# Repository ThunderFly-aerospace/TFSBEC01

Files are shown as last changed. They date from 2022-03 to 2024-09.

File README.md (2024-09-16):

# TFSBEC01 - High efficient power supply with measuring circuit for UAV

Many devices in unmanned vehicles require a quality power supply, and it is very useful to know the actual and real consumption of these components. Our TFSBEC module is designed to provide power to servos, autopilot (flight controller), and other medium-power drone accessories. In case the user needs more current or two independent sources on his drone, for example, a separate source for avionics and power-consuming elements (actuators), it is possible to chain these modules.

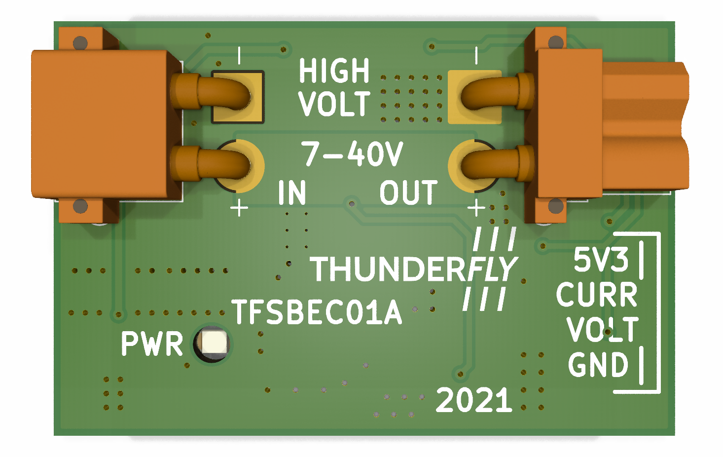
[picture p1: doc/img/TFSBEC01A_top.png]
TFSBEC01 top

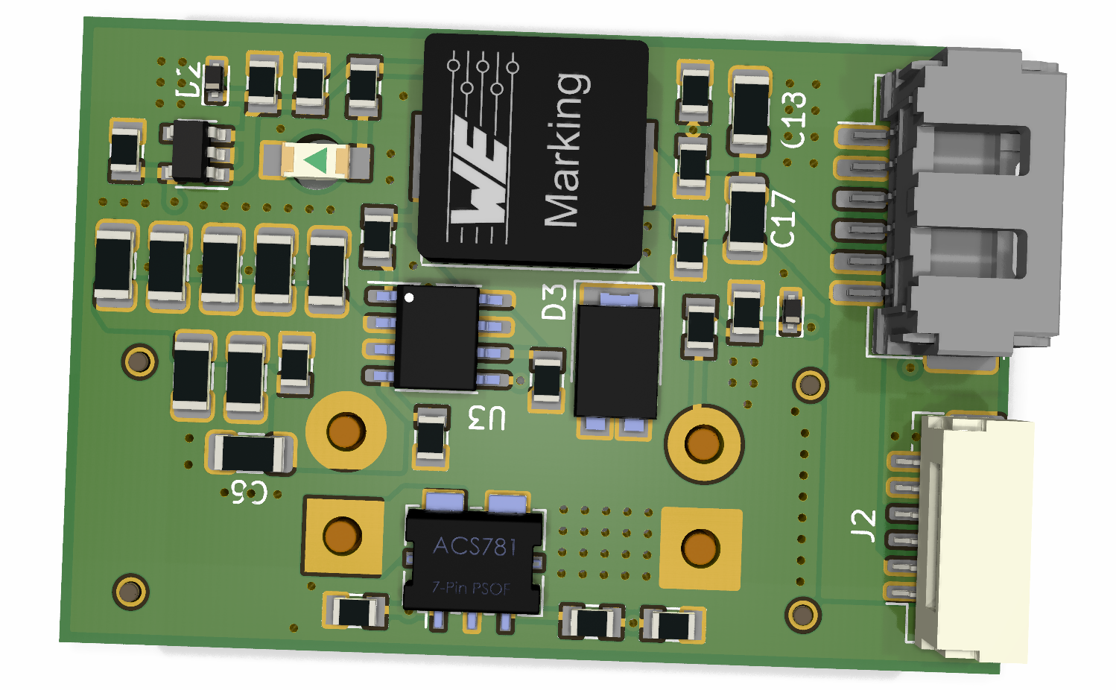
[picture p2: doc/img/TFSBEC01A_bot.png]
TFSBEC01 bottom


## Parameters

| Parameter | Value | Note |
|---|---|---|
| Regulator technology | Switched step-down| [LMR14050](https://www.ti.com/lit/ds/symlink/lmr14050.pdf)|
| Input voltage | 6 - 40 V  | Equivalent of 2S to 9S li-pol  accumulators |
| Output voltage | 5.4 V, 5 A | based form the PX4 standard, can be adjusted |
| Regulated connector | Molex Click-n-mat 6p, JST-GH 6p | Connectors are parallel |
| In/Out connector | XT30 | max current 15 A |
| Current measurement range | 0 - 50 A | |
| Volts per Amper | 39.6 mV/A | From component datasheet |
| Current measurement Volts offset | 330 mV | From component datasheet |
| Voltage measurement range | 0 - 40 V | Depend on target ADC max input ( max. 3.95 V ) |
| Voltage measurement divider | 10.13 | From schematic |
| Size | approx. 46 x 30 mm| PCB only |
| Weight | | PCB only |
| Compatibility | Pixhawk-based drones | As a quality source, it can be operated on any drone |

## PX4 Params

These constants are nominal values taken from the datasheet:

  * A = BAT1_A_PER_V = 25.2525
  * B = BAT_V_OFFS_CURR = 0.33
  * BAT1_V_DIV = 10.13
    
QGC build-in measurement can be used to estimate parameters more precisely for the specific piece. The PX4 estimation of current is calculated from the ADC raw voltage by the following formula: 

I estimate equation

For the computation of BAT_V_OFFS_CURR, multiple current measurements are usually needed, because there are significant peaks due to powering of electronics with a low current consumption.

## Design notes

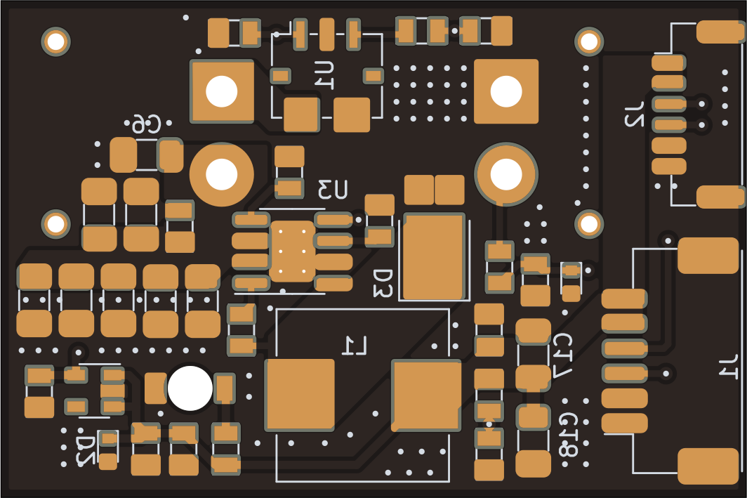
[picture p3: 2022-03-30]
doc/gen/img/pcb/TFSBEC01A-bottom.png

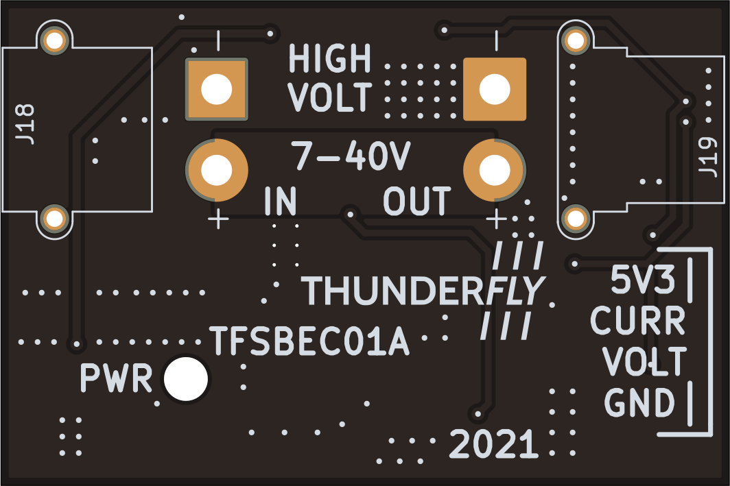
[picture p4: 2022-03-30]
doc/gen/img/pcb/TFSBEC01A-top.png

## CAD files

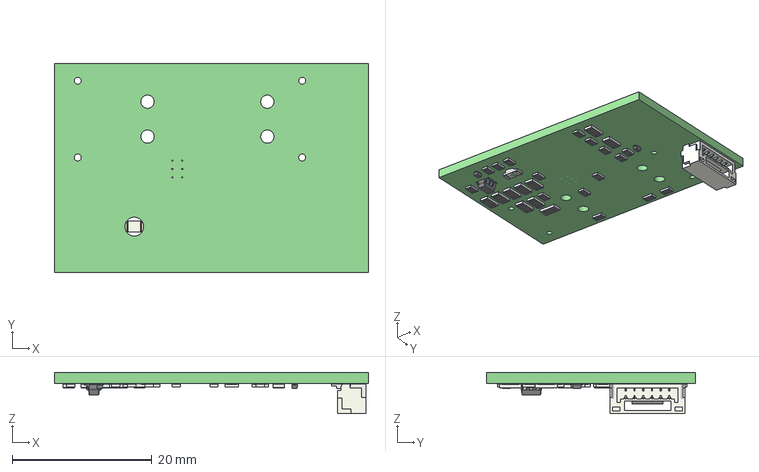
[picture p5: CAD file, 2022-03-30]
doc/gen/TFSBEC01A.step
45.0 x 30.0 x 5.89 mm
tmpdwvmqxz2 PCB

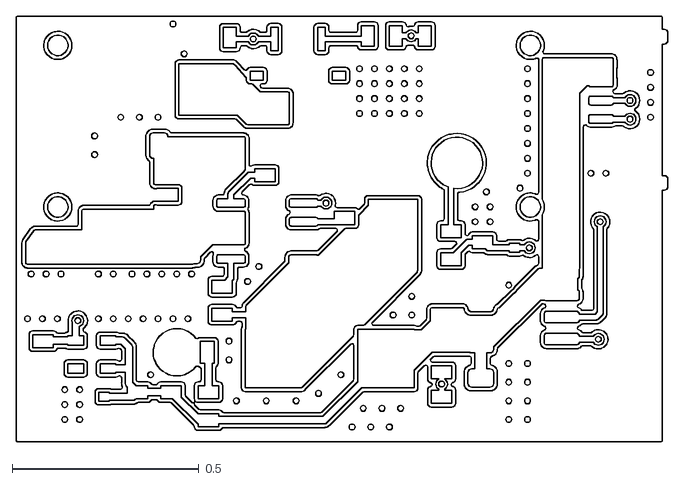
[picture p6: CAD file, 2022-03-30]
doc/gen/dxf/TFSBEC01A-B_Cu.dxf
1.75 x 1.14

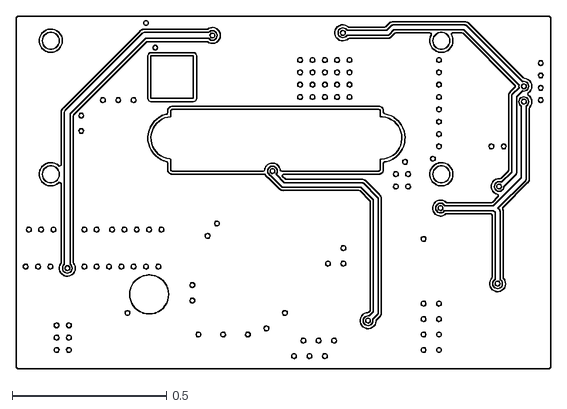
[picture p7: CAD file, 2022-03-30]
doc/gen/dxf/TFSBEC01A-F_Cu.dxf
1.73 x 1.14

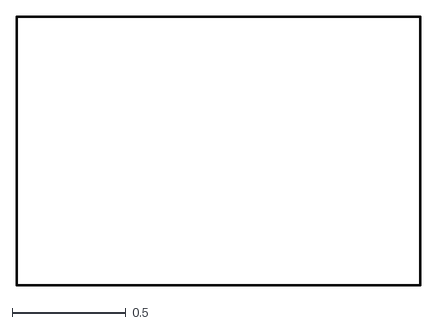
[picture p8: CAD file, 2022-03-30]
doc/gen/dxf/TFSBEC01A-Edge_Cuts.dxf
1.78 x 1.19

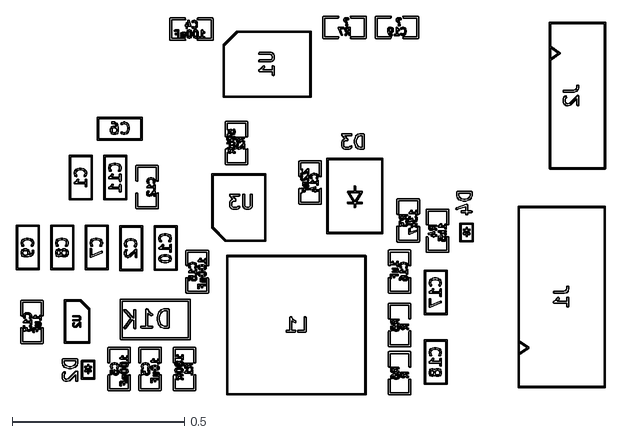
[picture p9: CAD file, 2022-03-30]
doc/gen/dxf/TFSBEC01A-B_Fab.dxf
1.71 x 1.10

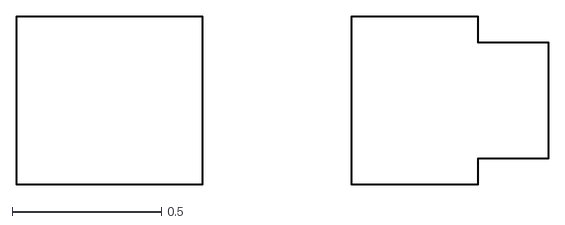
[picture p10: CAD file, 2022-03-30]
doc/gen/dxf/TFSBEC01A-F_Courtyard.dxf
1.79 x 0.565

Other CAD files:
doc/gen/dxf/TFSBEC01A-User_6.dxf
doc/gen/dxf/TFSBEC01A-User_4.dxf
doc/gen/dxf/TFSBEC01A-User_Drawings.dxf
doc/gen/dxf/TFSBEC01A-User_9.dxf
doc/gen/dxf/TFSBEC01A-User_Eco1.dxf
doc/gen/dxf/TFSBEC01A-User_8.dxf
doc/gen/dxf/TFSBEC01A-User_5.dxf
doc/gen/dxf/TFSBEC01A-User_7.dxf
doc/gen/dxf/TFSBEC01A-F_Adhesive.dxf
doc/gen/dxf/TFSBEC01A-Margin.dxf
doc/gen/dxf/TFSBEC01A-User_3.dxf
doc/gen/dxf/TFSBEC01A-User_Comments.dxf
doc/gen/dxf/TFSBEC01A-B_Adhesive.dxf
doc/gen/dxf/TFSBEC01A-B_Courtyard.dxf
doc/gen/dxf/TFSBEC01A-B_Mask.dxf
doc/gen/dxf/TFSBEC01A-B_Paste.dxf
doc/gen/dxf/TFSBEC01A-B_Silkscreen.dxf
doc/gen/dxf/TFSBEC01A-F_Fab.dxf
doc/gen/dxf/TFSBEC01A-F_Mask.dxf
doc/gen/dxf/TFSBEC01A-F_Paste.dxf
doc/gen/dxf/TFSBEC01A-F_Silkscreen.dxf
doc/gen/dxf/TFSBEC01A-User_1.dxf
doc/gen/dxf/TFSBEC01A-User_2.dxf
doc/gen/dxf/TFSBEC01A-User_Eco2.dxf

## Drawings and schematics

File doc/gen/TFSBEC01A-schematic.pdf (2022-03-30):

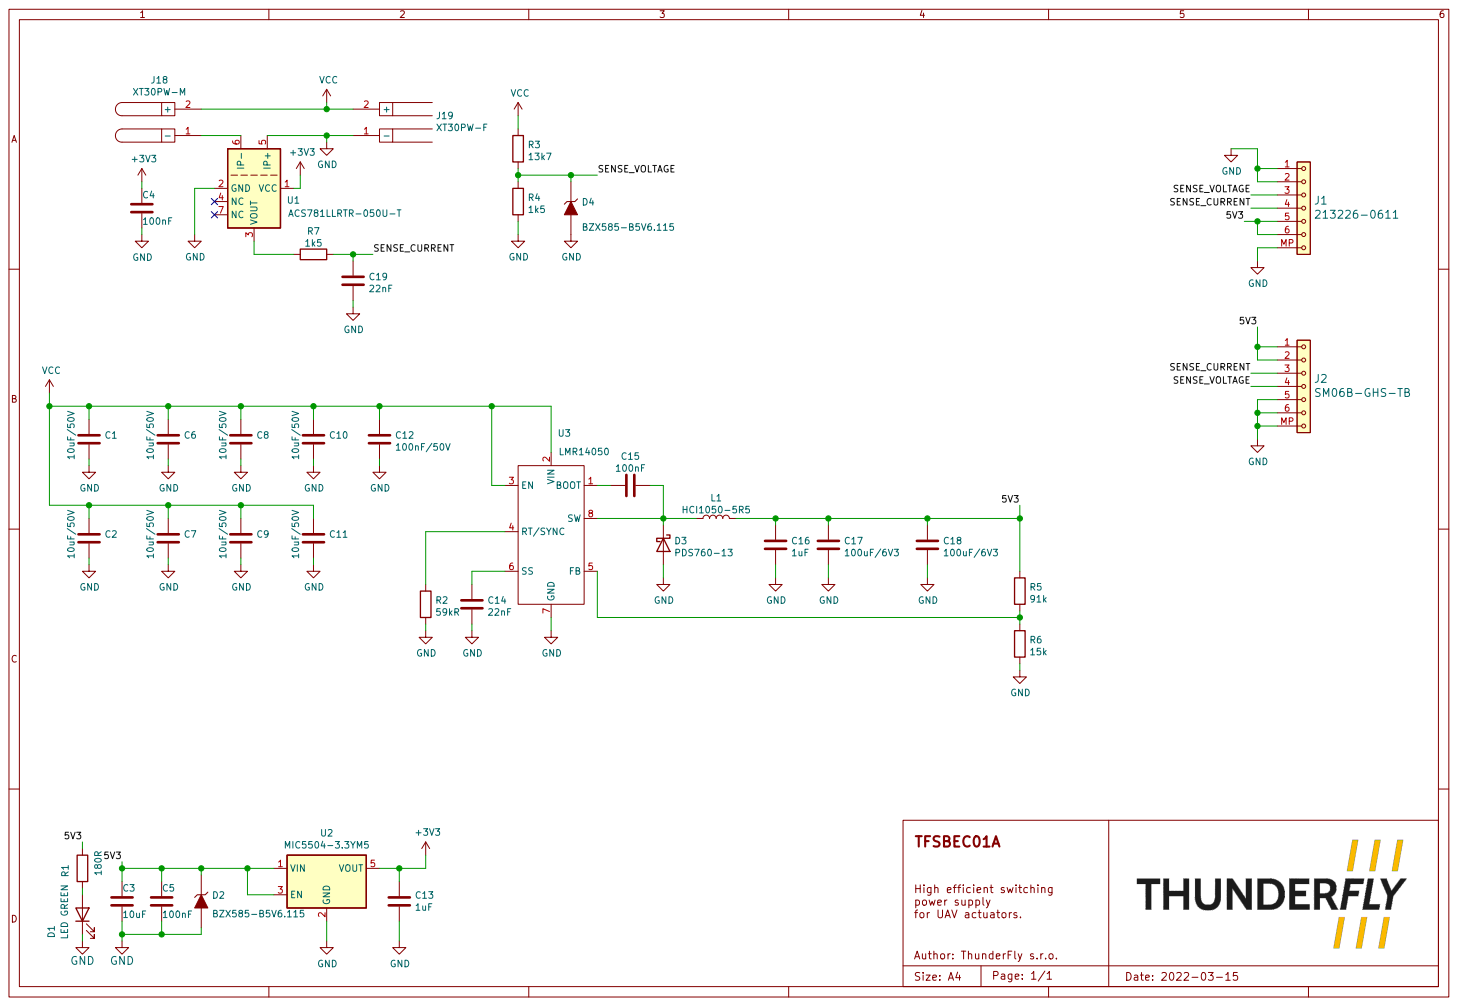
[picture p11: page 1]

2 EN 3 RT/SYNC 4 FB 5 SS 6 GND

for UAV actuators. GND

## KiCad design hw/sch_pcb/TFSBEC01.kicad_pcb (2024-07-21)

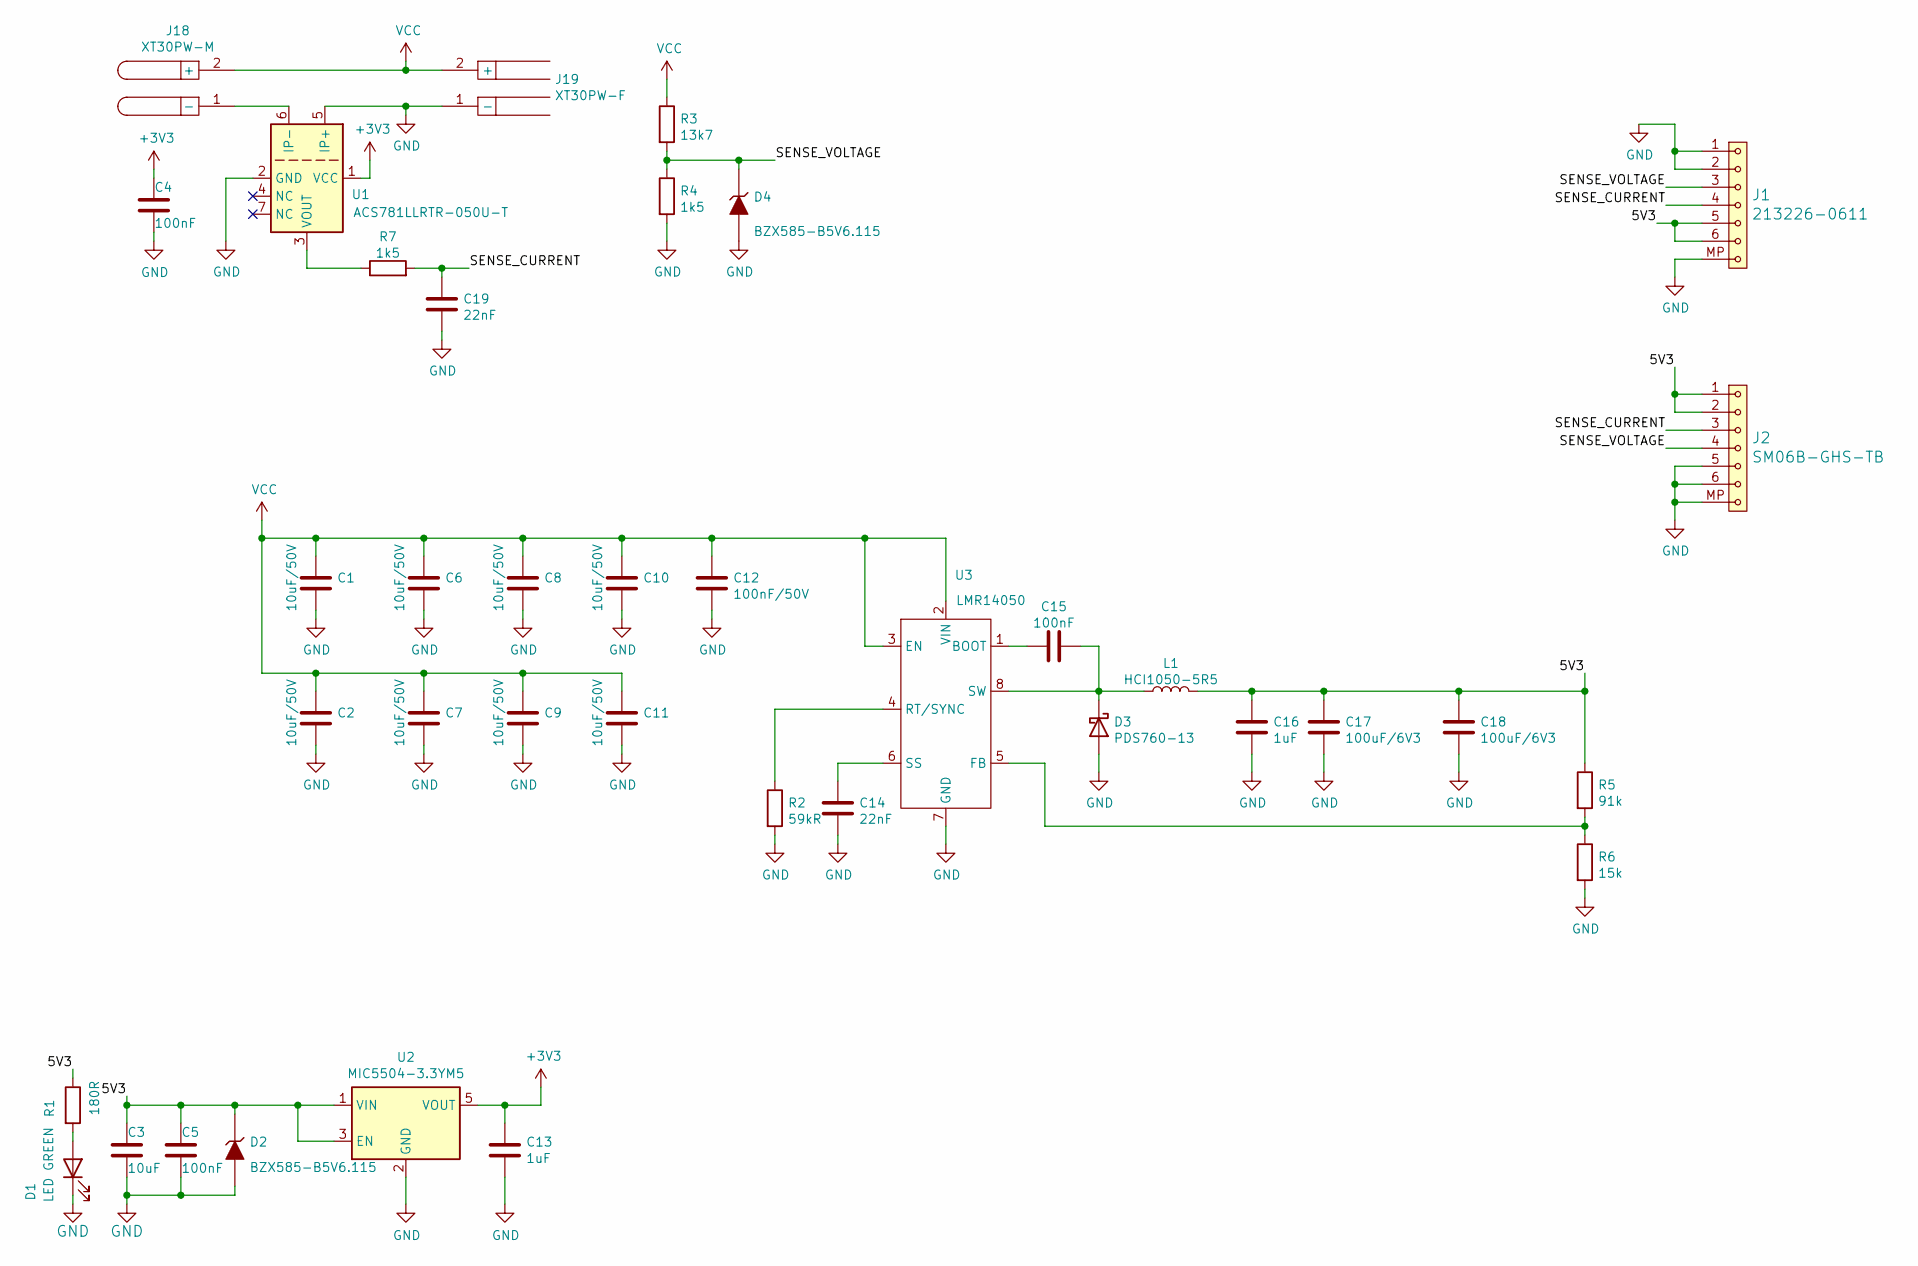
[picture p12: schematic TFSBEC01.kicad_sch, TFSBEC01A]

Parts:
C1, C2, C6, C7, C8, C9, C10, C11: 10uF/50V; R_1206_3216Metric
C3: 10uF; SMD-0805
C4, C5, C15: 100nF; SMD-0805
C12: 100nF/50V; SMD-0805
C13, C16: 1uF; SMD-0805
C14, C19: 22nF; SMD-0805
C17, C18: 100uF/6V3; R_1206_3216Metric
D1: LED GREEN; LED_1206
D2, D4: BZX585-B5V6.115; D_SOD-523
D3: PDS760-13; D_PowerDI-5
J1: 213226-0611; Molex_CLIK-Mate_505405-0670_1x06-1MP_P1.50mm_Vertical
J2: SM06B-GHS-TB; JST_GH_SM06B-GHS-TB_1x06-1MP_P1.25mm_Horizontal
J18: XT30PW-M; AMASS_XT30PW-M_1x02_P2.50mm_Horizontal
J19: XT30PW-F; AMASS_XT30PW-F_1x02_P2.50mm_Horizontal
L1: HCI1050-5R5; L_Wuerth_HCI-1050
R1: 180R; SMD-0805
R2: 59kR; SMD-0805
R3: 13k7; SMD-0805
R4, R7: 1k5; SMD-0805
R5: 91k; SMD-0805
R6: 15k; SMD-0805
U1: ACS781LLRTR-050U-T; Allegro_PSOF-7_4.8x6.4mm_P1.60mm
U2: MIC5504-3.3YM5; SOT-23-5
U3: LMR14050; SOIC-8-1EP_3.9x4.9mm_P1.27mm_EP2.41x3.3mm_ThermalVias

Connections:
+3V3: C4.1, C13.1, U1.1 (VCC), U2.5 (VOUT)
/5V3: C3.1, C5.1, C16.1, C17.1, C18.1, D2.1 (K), J1.5, J1.6, J2.1, J2.2, L1.2, R1.1, R5.1, U2.1 (VIN), U2.3 (EN)
/SENSE_CURRENT: C19.1, J1.4, J2.3, R7.2
/SENSE_VOLTAGE: D4.1 (K), J1.3, J2.4, R3.2, R4.1
GND: C1.2, C2.2, C3.2, C4.2, C5.2, C6.2, C7.2, C8.2, C9.2, C10.2, C11.2, C12.2, C13.2, C14.2, C16.2, C17.2, C18.2, C19.2, D1.1 (K), D2.2 (A), D3.2 (A), D4.2 (A), J1.1, J1.2, J1.MP, J2.5, J2.6, J2.MP, J19.1 (-), R2.2, R4.2, R6.2, U1.2 (GND), U1.5 (IP+), U2.2 (GND), U3.7 (GND), U3.9 (GND)
unnamed: C14.1, U3.6 (SS)
unnamed: C15.1, U3.1 (BOOT)
unnamed: C15.2, D3.1 (K), L1.1, U3.8 (SW)
unnamed: D1.2 (A), R1.2
unnamed: J18.1 (-), U1.6 (IP-)
unnamed: R2.1, U3.4 (RT/SYNC)
unnamed: R5.2, R6.1, U3.5 (FB)
unnamed: R7.1, U1.3 (VOUT)
VCC: C1.1, C2.1, C6.1, C7.1, C8.1, C9.1, C10.1, C11.1, C12.1, J18.2 (+), J19.2 (+), R3.1, U3.2 (VIN), U3.3 (EN)

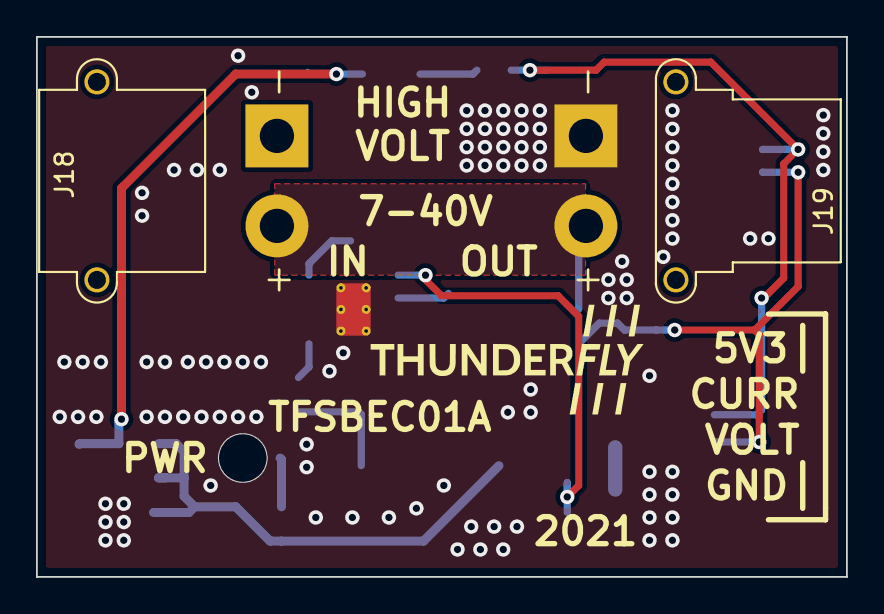
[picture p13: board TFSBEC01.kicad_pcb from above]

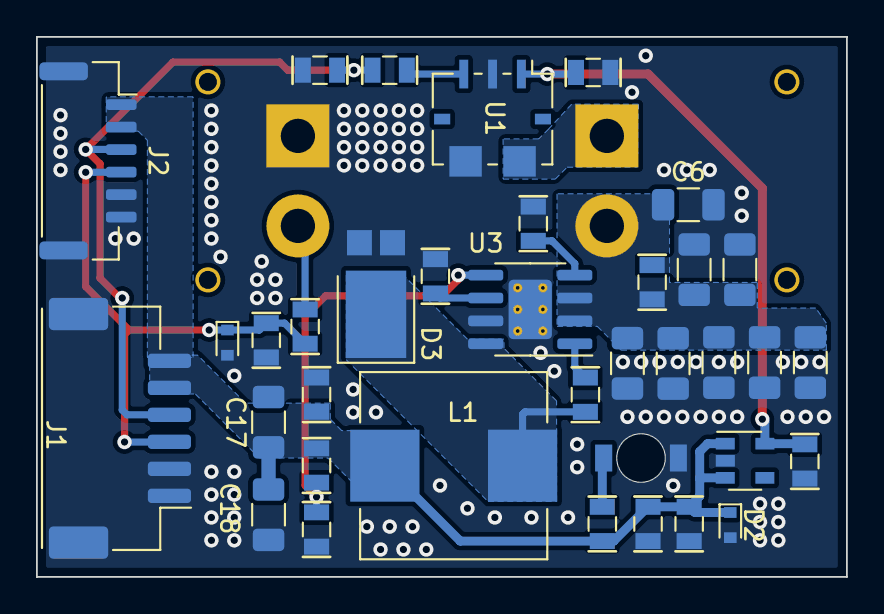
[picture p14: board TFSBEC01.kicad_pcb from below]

Board: 2 copper layers, 45.0 x 30.0 mm, 38 parts (36 on the bottom side), 14 nets.

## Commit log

2021-01-04 Tvorba schéma
    [TFSBEC01A.kicad_pcb, TFSBEC01A.kicad_sch]
2021-04-05 Title block update.
    [TFSBEC01A.kicad_sch]
2021-04-18 Edit shema
    [TFSBEC01A.kicad_sch]
2021-04-25 Edit PCB
    [TFSBEC01A.kicad_pcb, TFSBEC01A.kicad_sch]
2021-04-26 Add PCB dimensions.
    [TFSBEC01A.kicad_pcb]
2022-03-15 Update project to KiCAD 6.0. Update title block.
    [TFSBEC01A.kicad_pcb, TFSBEC01A.kicad_sch]
2022-03-30 Update actions products
    [TFSBEC01A-B_Cu.gbr, TFSBEC01A-B_Mask.gbr, TFSBEC01A-B_Paste.gbr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]
2023-10-07 Convert to KiCAD7 Improve schematics layout Add link to datasheet.
    [TFSBEC01A.kicad_pcb, TFSBEC01A.kicad_sch]
2023-10-07 Remove revision from project files name.
    [TFSBEC01.csv, TFSBEC01.kicad_pcb, TFSBEC01.kicad_sch]
2023-10-07 switched dimensions to comments layer.
    [TFSBEC01.kicad_pcb, TFSBEC01.kicad_sch]
2024-07-21 Update to KiCADv8. Improve documentation.
    [TFSBEC01.csv, TFSBEC01.kicad_pcb, TFSBEC01.kicad_sch]
